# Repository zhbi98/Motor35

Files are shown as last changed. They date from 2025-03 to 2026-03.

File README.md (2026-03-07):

# Motor35

转速-扭矩特性步进电机运用普通的开环控制方式在低速和低负载的情况下可以保持较好的控制精度，但随着负载增大或转速度增加会发生丢步，另一个是转速-扭矩特性让步进电机无法在高转速下稳定工作。

## 特性

在低速状态下，步进电机的扭矩特性曲线通常为水平直线，能够提供较高的扭矩。在高速状态下，由于电感的影响，扭矩特性曲线呈指数下降，导致电机的负载能力显著降低。

> **最大扭矩：** 最大扭矩出现在中低转速范围，随着转速的提高，扭矩会逐渐下降。因为在高频率下，电流流动受到绕组电感的影响，导致电流无法达到稳定值，从而扭矩降低。
> 
> **启动扭矩与连续扭矩：** 启动扭矩指在启动时能够提供的最大扭矩，而连续扭矩则指电机持续运行时能够维持的扭矩。随着脉冲频率的增加，启动扭矩和连续扭矩都会下降。

## 闭环

闭环控制是在开环控制的基础上，增加了 **反馈检测环节**（例如在电机轴增加编码器），形成指令-执行-位置检测-修正的闭环逻辑。解决存在的丢步、偏差、抗干扰能力弱问题，还能提升系统和容错能力。

## FOC 控制

混合式步进电机与无刷电机的内在联系（结构定义相似性，工作原理相似性），所以可以用无刷电机 FOC 的驱动思想驱动步进电机。

结构方面：永磁转子+定子绕组的结构，定子方面：两者都有多相绕组（步进电机通常为两相，无刷电机通常为三相），转子方面：都采用永磁材料制造转子磁极，无刷设计：两者都没有电刷和机械换向器，依靠电子换向。

对于两相步进电机，虽然只有两个绕组，但通常两相绕组是正交的，从而可以简化步骤，省略我们的 clarke 变换，所以其余同样可以采用类似的思路进行一个电流环FOC控制。

    电流检测：对 AB 两相电流进行检测
    Park变换：将 AB 轴静止系转换为dq轴旋转坐标系
    PI调节器：对 Id 和 Iq 进行控制
    Invpark变换：讲 dq 轴转换为AB轴
    SVPWM调制: 输出占空比
    双 H桥驱动：驱动我们的步进电机

这些可以整合到一个驱动器中实现，如下图。这就是一体化集成步进电机闭环驱动器。板上集成磁编码器，具有速度，位置，电流闭环控制功能，适用于 3D 打印机，小型机械臂。

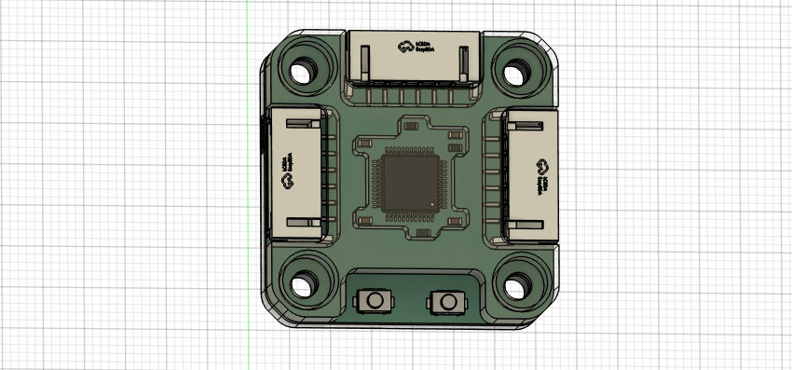
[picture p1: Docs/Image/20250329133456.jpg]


## 硬件

(1) 2 相逆变功率级：东芝凌耐压 50V，载流3.5A 的 PWM 斩波式双全桥电机驱动器，内置带低导通电阻的输出MOSFET（基于成本考虑可以选择其他的型号）。

(2) RS485 收发器：TI 德州仪器 SN75176B（基于成本考虑可以选择其他的型号）。

(3) CAN2.0B 收发器：NXP 恩智浦 High-speed CAN transceiver TJA1051（基于成本考虑可以选择其他的型号）。

(4) 磁编码器：MagnTek 麦歌恩 mt6816 单圈绝对式14位编码器，支持最高转速25Krpm。

(6) 主控 MUC 芯片：意法半导体 STM32F103。

## 关于打样

驱动器板 Motor35（PCB 采用 **4 层板** 设计）：[HardWare/kiacd_project](./HardWare/kiacd_project)

如果想自己修改 PCB 需要安装 KiCad（开源的 EDA 工具，也非常易学），官方下载地址： https://www.kicad.org/。

打样制作可以直接进入到下面这两个路径下：

把 Motor35 Gerber 文件夹 [HardWare/Gerber](./Docs/Motor35-PCB/) 压缩为 Motor35.zip，

把这个 .zip 给 PCB 制造厂即可（例如 JLC，**PCB 经过打样验证，可以放心使用**）。

**器件 BOM 目录**：[HardWare/ibom.html](./Docs/Motor35-BOM.csv)（PCB 没器件位号，按网页交互式 BOM 贴片）。

原理图 PDF 目录： [Docs/Motor35-SCH.csv](Docs/Motor35-SCH.pdf)

## 核心固件

固件主要包括几大功能模块：

- hal 驱动：板载的各种硬件驱动比如 USB、Tim、Can、Spi。
- utils 库：STM32 的 Flash 存储接口，Modbus 协议解析库，软定时器组件。
- drivers：ARM的CMSIS驱动，ST官方的HAL库。
- device：电机H桥驱动，编码器驱动和校准，电机控制核心代码，LED 驱动框架 LedMX 和按键驱动 MultiButton。
- main：上层 Can，Rs485 应用控制协议，用于控制同步电机状态/参数，以及用户设置参数保存功能。

## 编译下载

固件没有使用 ARM Keil 开发，而是先用 CMake 构建出 Makefile，然后再用 arm-gcc 编译（可以自己创建 F103 的 Keil 工程，把 Motor35 组织到 Keil 编译）。

Motor35 用的是 VSCode 搭配 OpenOCD 图形化下载调试，需要下载安装下列工具链：

MiniGW： https://sourceforge.net/projects/mingw-w64/files/

arm-gcc ：[Downloads | GNU Arm Embedded Toolchain Downloads – Arm Developer](https://developer.arm.com/downloads/-/gnu-rm)

openOCD：[Download OpenOCD for Windows](https://gnutoolchains.com/arm-eabi/openocd/)

CMake：[Download CMake](https://cmake.org/download/)

VSCode：[https://code.visualstudio.com/](https://code.visualstudio.com/)

> 安装后具体如何配置使用这些工具，篇幅较长不写在这里，我把具体配置使用方法写在这里：[工具链配置使用方法](https://blog.csdn.net/jf_52001760/article/details/126826393)。

**Motor35 编译步骤**：

把 cmake 脚本 CMakeLists.txt 的目录添加到 `1` 这里，如下图。

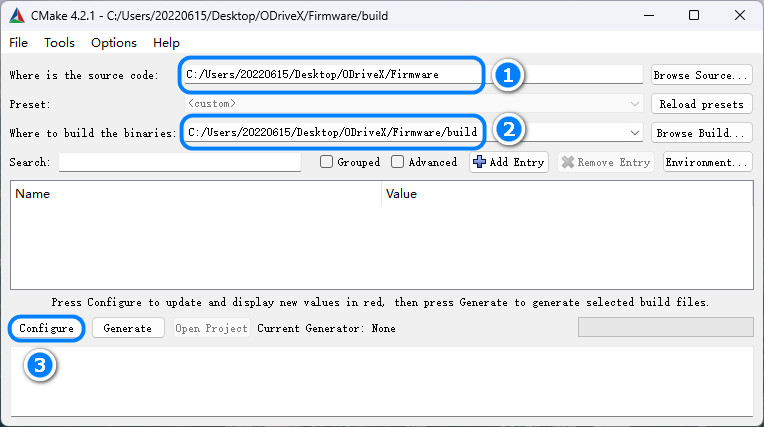
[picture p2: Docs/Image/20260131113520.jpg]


(2) 在 Firmware 目录下创建 build 目录，并指定到 `2` 这里。

(3) 点击 "Configure"，在弹出面板选择目标工程，如下图。

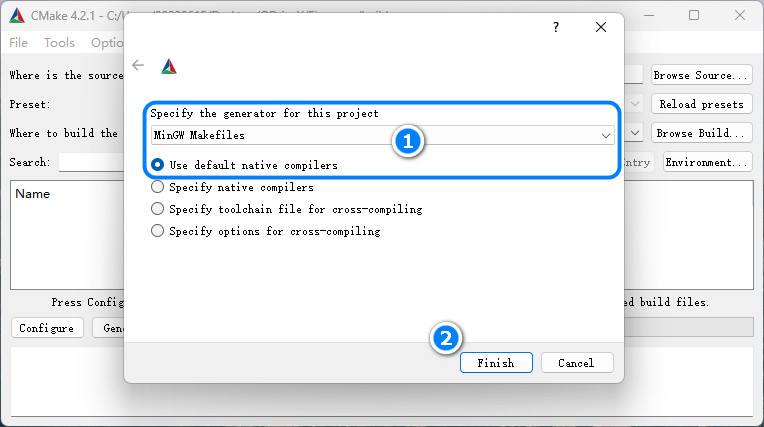
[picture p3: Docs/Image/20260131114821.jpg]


(5) 在 vscode 的命令行 `cd build` 进入`build/`目录，然后执行 make -j2 即可开始编译。

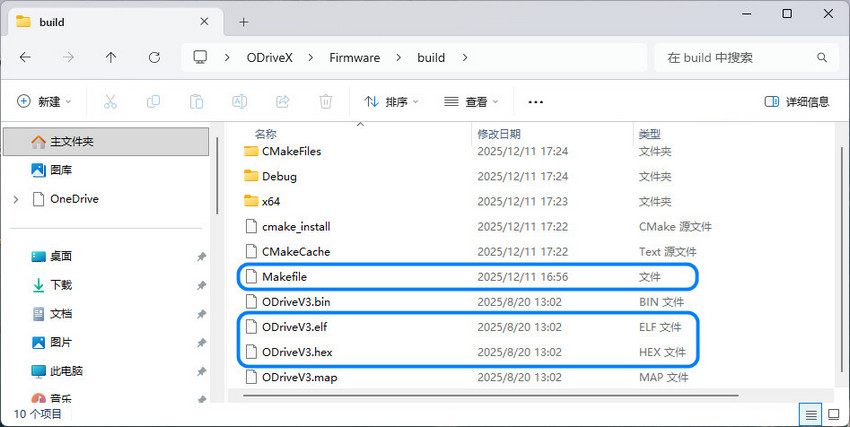
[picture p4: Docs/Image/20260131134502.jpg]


(6) 使用 openOCD 把 `.elf` 文件下载到 Motor35 硬件，下载方法同样参照 [工具链配置使用方法](https://blog.csdn.net/jf_52001760/article/details/126826393)（PCB 上预留了 SWD 调试接口同时支持固件下载）。

## 电机选型

电机可以在淘宝搜索购买，最好购买低相电阻步进电机（较好的电机的相电阻通常为 2-5 Ohm）。相电阻过高可能导致电机在静止时出现高频震动。

电机机身：28MM，出轴直径：5MM (D轴4.5MM)，出轴长度：22MM
静力矩：0.29 N.m，额定电流：1.5 A，电阻：3.0Ohm/相。

> 要实际测量电机相电阻（万用表接到对应相的两个端子测量），比如购买的步进电机在参数描述中标明的相电阻为 2.2 Ohm，实则实际测出的相电阻高达 29 Ohm
> 
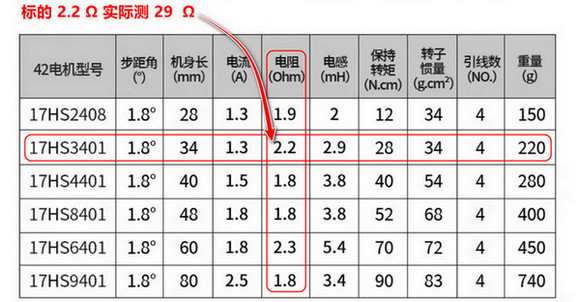
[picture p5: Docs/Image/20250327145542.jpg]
> 

## 编码器安装

在电机轴上安装径向磁铁（用于磁编码器检测），磁铁尺寸 $d=8mm$，$h=2mm$，注意径向磁铁和轴同心度不要过度偏移，让后把驱动器板放到板支架中，用 M3.0 螺丝把驱动器和板定到电机尾部，磁铁与编码器的间隙大概为 $1mm$。

驱动板支架零件目录：[Model](./Model)，把 .step 文件给 3D 打印即可。

## Configuration

固件上已经调试好 Pid 参数，可以适配大多数35步进电机，默认情况下不需要再调试 Pid 电机也能正常工作。Pid 可以用 Can 指令调整（看Can协议部分的说明），方法如下：

- **Kp 的调整**：将 Kd，Ki 置 0，从零开始逐渐增加 Kp，直到系统出现震荡。然后逐渐减小Kp，直到系统不再震荡。Kp 的最终值通常在引起震荡的 Kp 值的 80%-90% 之间。

- **Kd 的调整**：在 Kp 调整稳定后，开始增加 Kd。如果系统在空载时仅需要 Kp，那么在负载情况下可能需要增加 Kd 来减少超调和震荡。

- **Ki 的调整**：如果系统在 Kp 和 Kd 的调整后仍然存在静态误差，可以尝试增加 Ki。但 Ki的值通常很小，需要细致地调整。

配置限制参数，限制参数再 /motor/control_config.h 文件定义，如下。

```c
/********************  硬件配置区  ********************/
#define _Current_Rated_Current  (3000)  /**< 额定电流(mA)*/
#define _Current_Cali_Current   (2000)  /**< 校准电流(mA)*/
/********************  运动参数配置区  ********************/
...
#define _Move_Rated_Speed           ((int32_t)(50 * Move_Pulse_NUM))    /**< (额定转速)(50转每秒)*/
#define _Move_Rated_UpAcc           ((int32_t)(1000 * Move_Pulse_NUM))  /**< (固件额定加速加速度)(1000r/ss)*/
#define _Move_Rated_DownAcc         ((int32_t)(1000 * Move_Pulse_NUM))  /**(固件额定减速加速度)(1000r/ss)*/
#define _Move_Rated_UpCurrentRate   ((int32_t)(20 * _Current_Rated_Current))    /**< (固件额定增流梯度)(20倍额定/s)*/
#define _Move_Rated_DownCurrentRate ((int32_t)(20 * _Current_Rated_Current))    /**< (固件额定减流梯度)(20倍额定/s)*/
```

用户设置在 /main/setup/setup.c 中定义，用户设置参数可以用 Can 指令设置（看Can协议部分的说明）设置后保存在 Flash 掉电保存。

```c
const _setup_t _setup_def = {
    ...
    .can_id = 0x01,
    .home_ofs = 0,
    ...
    .current_down_acc = 2 * 1000, /*(mA/s)*/
    .current_up_acc = 2 * 1000, /*(mA/s)*/
    .current_rated = 1000,
    .cali_current = 2000,
    ...
};
```

## 按键逻辑

(1) 启动停止闭环模式：按键 1 短按一次，启动或停止闭环模式，启动闭环模式的同时会进入默认的模式，例如位置闭环。

(2) 目标清 0：按键 2 短按一次，如果当前控制模式为速度模式，那么按下此时会将目标速度置为 0，位置模式，则将目标位置置为 0。

(3) 电机编码器校准：按键 1 长按两次，校准时电机会慢速正转一圈再反转一圈。

> 按下按键时 LED 跟随闪烁，以指示按键是否响应。

## CAN 协议

一帧 CAN 报文只能传 8 个字节数据，和 11 位的标准 Std-Id，这里把 Std-Id 的低 7 位也用作数据，用来传控制指令字 CMD，控制协议定义如下：



Device Id 占用 4 位，CMD 占用 7 位，协议最多两个参数：参数 1 占用 4 个字节，参数 2 占用 4 个字节。

> 个别协议要两个参数，例如位置控制：设置目标位置和速度限制。

具体指令在[protocols/can_protocol.c](./Firmware/main/protocols/can_protocol.c) 这里定义，具体可以看这个文件，具体控制指令和控制方式查看 [Docs/Protocols](./Docs/Protocols) 目录下相应的协议文档，这里只截取部分。

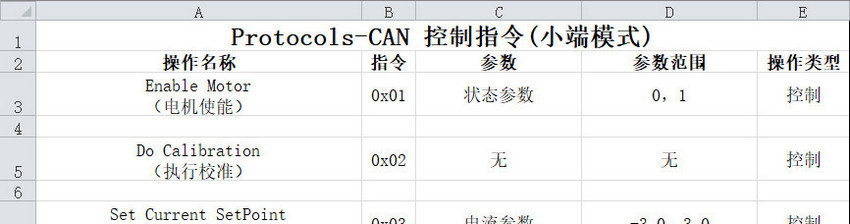
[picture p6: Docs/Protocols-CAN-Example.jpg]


## 震动问题

注意步进驱动器控制步进电机工作在位置环并要求静止在某个固定位置时可能会出现高频震动的问题。引起高频微弱震动的原因是由于在位置环控制模式下，驱动器为了让让电机接近指定位置而控制电机在齿槽间反复微调而产生震动。

> 这个现象排除驱动器的电路问题（比如焊接的电流采样电阻是否正确等等），磁编码器检测磁铁的安装同心度问题（通常同心度要求不是很高，确保不要过度偏移即可）那有极大的可能是步进电机的相电阻过大导致的，可以更换了其他电机进行测试。

如果更换电机测试后发现同一个闭环步进电机驱动器驱动一个步进电机工作在位置环保持静止时工作正常，而驱动另一个步进电机静止时出现高频震动，那可以肯定就是相电阻过高而导致的。出现震动现象的电机相电阻通常为 10-30 Ohm，而较好电机的相电阻通常为 2-5 Ohm。注意检查电机参数可能的虚标，例如购买的步进电机在参数描述中标明的相电阻为 2.2 Ohm，实则实际测出的相电阻高达 29 Ohm，所以电机出现震动现象和线圈相电阻是有一定关系的。

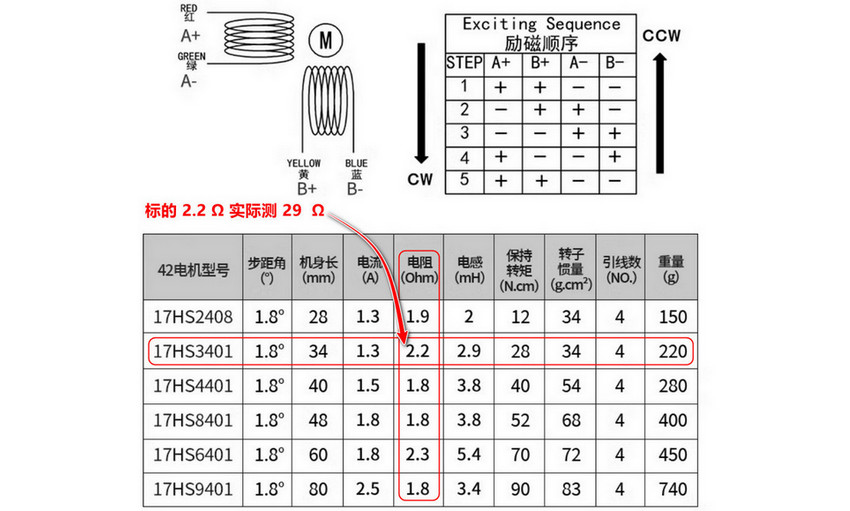
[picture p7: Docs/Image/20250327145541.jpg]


可以通过修改驱动器程序固件来修复这个问题，修改驱动输出部分，在最终 FOC 输出驱动电流部分添加一个系数即可，通过该系数来调节驱动器 FOC 的输出电流（当然调节电流参数会对最终的扭矩有略微的影响，但并不影响闭环精度），如下图。

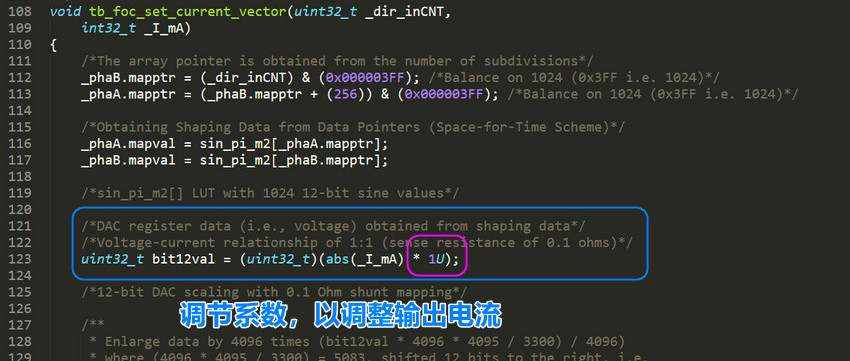
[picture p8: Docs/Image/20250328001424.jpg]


## 控制带宽

电机控制速度/位置积分需要精确节拍，电机控制所有逻辑都是在定时器触发的中断中进行，我设置的中断函数频率较高，达到20KHz，可能会导致 main 主循环不执行。

> **20 kHz 中断**：TIM 每 50 μs 触发一次中断。

**电机控制逻辑较多：** 运行时间合计接近或超过 50 μs，会形成中断几乎连轴转、主循环几乎没机会跑”的情况（和芯片主频无关，只要中断内处理的时间超过中断周期时间就会导致 main 函数不执行）。

> 通过 SPI 阻塞读 MT6816，最多 3 次尝试 × 2 次 16bit 传输，再加 16 位奇偶校验循环。SPI 时钟为 9MHz，仅通信就可能 5-15μs。
> 
> 编码器处理、位置/速度估计、多种运行模式下的控制（DCE/PID/电流等）、运动规划、软目标更新、堵转/过载检测等就需要数十μs。

没有具体要求需要多少控制频率，控制制带宽越高，控制越平滑所以默认设定为 20KHz，若控制带宽允许，可把闭环控制改为 10 kHz 或 5 kHz，中断周期变为 100 μs / 200 μs。

> 这里 20 kHz 不是控制带宽的硬性要求，更多是裕量和步进分辨率。

修改控制频率同时改两处：
motion_planner.h 的  CONTROL_FREQUENCY 定义。
修改电机控制运行中断定时器的中断时间。

```c
/****************************************  控制器频率配置区  ****************************************/
#define CONTROL_FREQ_HZ   (20000)                     /**< 控制频率_hz*/
#define CONTROL_PERIOD_US (1000000 / CONTROL_FREQ_HZ) /**< 控制周期_us*/
```

### 评估控制带宽

(1) motor_control.c 涉及的一阶滤波：由 `等效时间常数由 >> 5`（约 32 个采样）决定。20 kHz 时：32 × 50us =1.6 ms 即控制带宽约 100 Hz。对很多应用来说 50 Hz 左右就足够。

(2) 位置/速度环 (DCE、PID 闭环带宽)：这是外环（位置环、速度环），一般做到几十到一两百 Hz 带宽就足够（位置/速度环 -3 dB 带宽）。 

> 常见经验：**采样率 ≥ 10～20 倍闭环带宽**。 
> 若你目标闭环带宽在 100～200 Hz，**5 kHz 已经够用，2 kHz 是底线**。

(3) FOC/电流指令：由 TB67H450 等驱动接收，5～10 kHz 更新电流给定对多数应用足够。

(4) 运动规划：用 CONTROL_FREQUENCY 做离散积分，频率高一点更平滑，但 5～10 kHz 通常足够平滑。

(5) 控制更新频率：下限约 2～5 kHz（再低速度估计和环路的相位裕量会变差）。推荐 5～10 kHz 在保证控制性能的同时，能给主循环留出明显时间。在需要 **极高步进率** 或 **尽量小的相位延迟** 时才必要 20 kHz。

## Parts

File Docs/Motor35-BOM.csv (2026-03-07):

Reference | Value | Datasheet | Footprint | Qty | DNP
C1,C3,C5,C7,C10,C11,C16 | 0.1uF | ~ | Capacitor_SMD:C_0603_1608Metric | 7
C2,C6 | 22pF | ~ | Capacitor_SMD:C_0603_1608Metric | 2
C4,C8,C17,C26,C31 | 10uF | ~ | Capacitor_SMD:C_0603_1608Metric | 5
C12,C13,C14,C15 | 100nF (104) 10% 50V | ~ | Capacitor_SMD:C_0603_1608Metric | 4
C18 | 100pF(101) 50V | ~ | Capacitor_SMD:C_0603_1608Metric | 1
C19,C20 | 100nF(104) 50V | ~ | Capacitor_SMD:C_0603_1608Metric | 2
C21 | 100nF104 | ~ | Capacitor_SMD:C_0603_1608Metric | 1
C22 | 4.7uF(475) 50V | ~ | Capacitor_SMD:C_1206_3216Metric | 1
C23 | 10uF(106) | ~ | Capacitor_SMD:C_0603_1608Metric | 1
C24 | 47uF(106) | ~ | Capacitor_SMD:C_0603_1608Metric | 1
C27,C28,C29,C30 | 100uF 50V | ~ | Capacitor_SMD:C_1206_3216Metric | 4
C32 | 100nF | ~ | Capacitor_SMD:C_0603_1608Metric | 1
D1 | RED LED | ~ | LED_SMD:LED_0603_1608Metric | 1
D2,D3 | B5819WS | http://www.vishay.com/docs/85622/1n914.pdf | Diode_SMD:D_0805_2012Metric | 2
D4 | SS54 | http://www.vishay.com/docs/85622/1n914.pdf | Diode_SMD:D_SMA | 1
D5 | SMBJ28CA | https://www.vishay.com/docs/88301/15ke.pdf | Diode_SMD:D_SMB | 1
IC1,IC2 | TB67H450FNG,EL | http://toshiba.semicon-storage.com/info/docget.jsp?did=65346&prodName=TB67H450FNG | 3rd_Driver_Motor:SOIC-8_L4.8-W5.8-P1.27_TB67H450FNG | 2
IC3 | MT6816 | http://www.magntek.com.cn/upload/MT6816_Rev.2.0.pdf | 3rd_Sensor_Encoder:SOIC-8_L4.7-W5.8-P1.27_MT6816 | 1
IC4 | ME3116AM6G | https://componentsearchengine.com/Datasheets/1/ME3116AM6G.pdf | 3rd_Converter_DCDC:SOT-23-6_L2.7-W2.2-P0.95_ME3116AM6G | 1
J1 | DBUG |  | 3rd_Connector_JST_SMD:CONN-SMD_1x3P-P1.0-H_WAFER-SH1.0-3PWB | 1
J2 | SWD |  | 3rd_Connector_JST_SMD:CONN-SMD_1x4P-P1.0-H_WAFER-SH1.0-4PWB | 1
J3,J7 | CAN_BUS |  | 3rd_Connector_JST_SMD:CONN-SMD_1x2P-P1.0-H_WAFER-SH1.0-2PWB | 2
J4 | MOTOR |  | 3rd_Connector_JST_SMD:CONN-SMD_1x6P-P2.0-H_WAFER-PH2.0-6PWB | 1
J5,J6 | POWER IN |  | 3rd_Connector_JST_SMD:CONN-SMD_1x6P-P2.0-H_WAFER-PH2.0-6PWB | 2
JP1 | Jump | ~ | Jumper:SolderJumper-2_P1.3mm_Open_RoundedPad1.0x1.5mm | 1
L1 | FCI3216-6R8 6.8uH | ~ | Inductor_SMD:L_1206_3216Metric | 1
R1 | 10M | ~ | Resistor_SMD:R_0603_1608Metric | 1
R2 | 3.3K | ~ | Resistor_SMD:R_0603_1608Metric | 1
R5,R9,R10,TH1 | 10K | ~ | Resistor_SMD:R_0603_1608Metric | 4
R8 | 1k | ~ | Resistor_SMD:R_0603_1608Metric | 1
R11,R12,R13,R14 | 1KΩ (1001) ±1% | ~ | Resistor_SMD:R_0603_1608Metric | 4
R15,R16 | 0.1Ω (R100) ±1% | ~ | Resistor_SMD:R_1206_3216Metric | 2
R17 | 1.91k(1901) | ~ | Resistor_SMD:R_0603_1608Metric | 1
R18 | 10k(1002) | ~ | Resistor_SMD:R_0603_1608Metric | 1
R19 | 1M | ~ | Resistor_SMD:R_0603_1608Metric | 1
R22 | 120R | ~ | Resistor_SMD:R_0603_1608Metric | 1
S1,S2 | KEY-PB_4P_MIN |  | 3rd_Button_Switch_SMD:KEY-SMD_2P_L4.0-W3.0-V_K2-1807SN-A3DW-06 | 2
U1 | XC6206P332MR | https://www.torexsemi.com/file/xc6206/XC6206.pdf | Package_TO_SOT_SMD:SOT-23 | 1
U2 | STM32F103CBTx | https://www.st.com/resource/en/datasheet/stm32f103cb.pdf | Package_QFP:LQFP-48_7x7mm_P0.5mm | 1
U3 | TJA1051T |  | 3rd_Interface_CAN:SOT96_L5.0-W4.0-P1.27_TJA1051 | 1
Y1 | 3225 8M 12PF 10PPM | ~ | Crystal:Crystal_SMD_3225-4Pin_3.2x2.5mm | 1

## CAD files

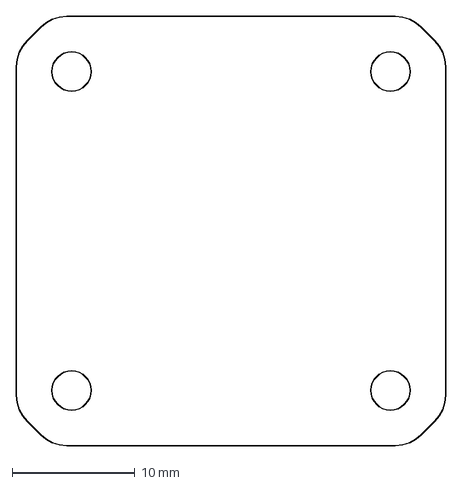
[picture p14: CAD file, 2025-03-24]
HardWare/EDG.dxf
35.0 x 35.0 mm

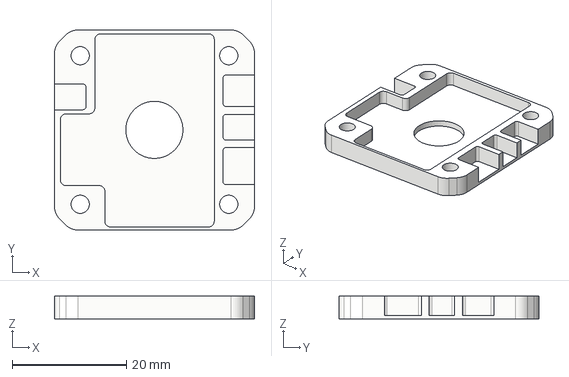
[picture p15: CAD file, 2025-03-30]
Model/Motor35SUP.step
35.0 x 35.0 x 4.00 mm

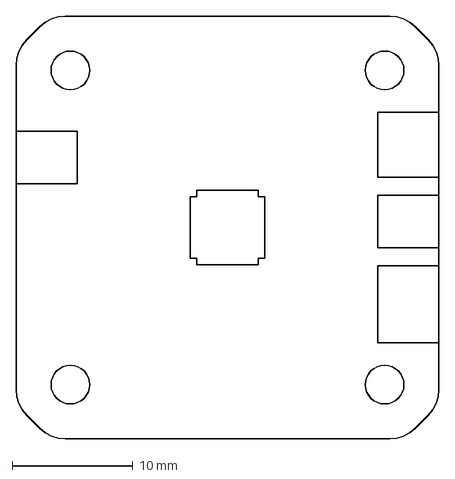
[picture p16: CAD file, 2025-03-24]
HardWare/BOM.dxf
35.0 x 35.0 mm

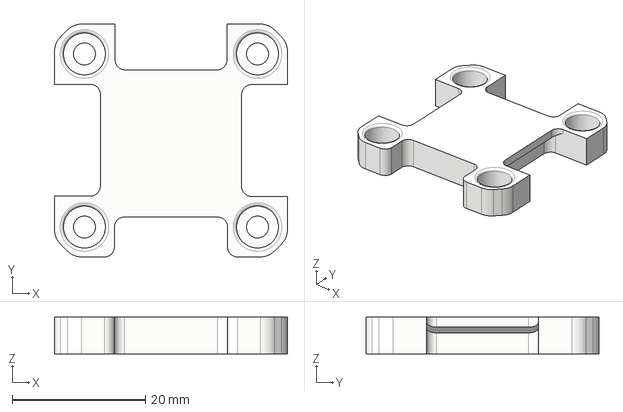
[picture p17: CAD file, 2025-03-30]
Model/Motor35OVER.step
35.0 x 35.0 x 5.55 mm

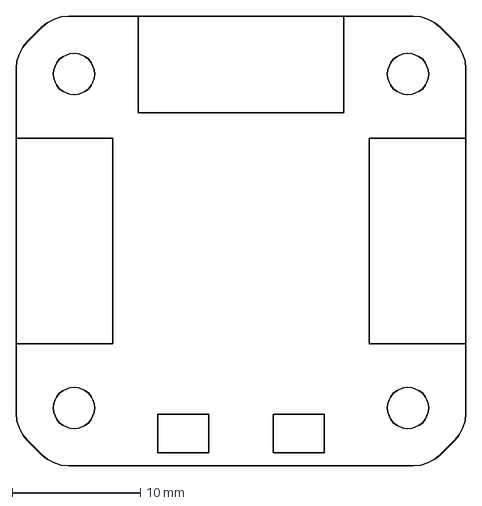
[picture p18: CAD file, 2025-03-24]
HardWare/TOP.dxf
35.0 x 35.0 mm

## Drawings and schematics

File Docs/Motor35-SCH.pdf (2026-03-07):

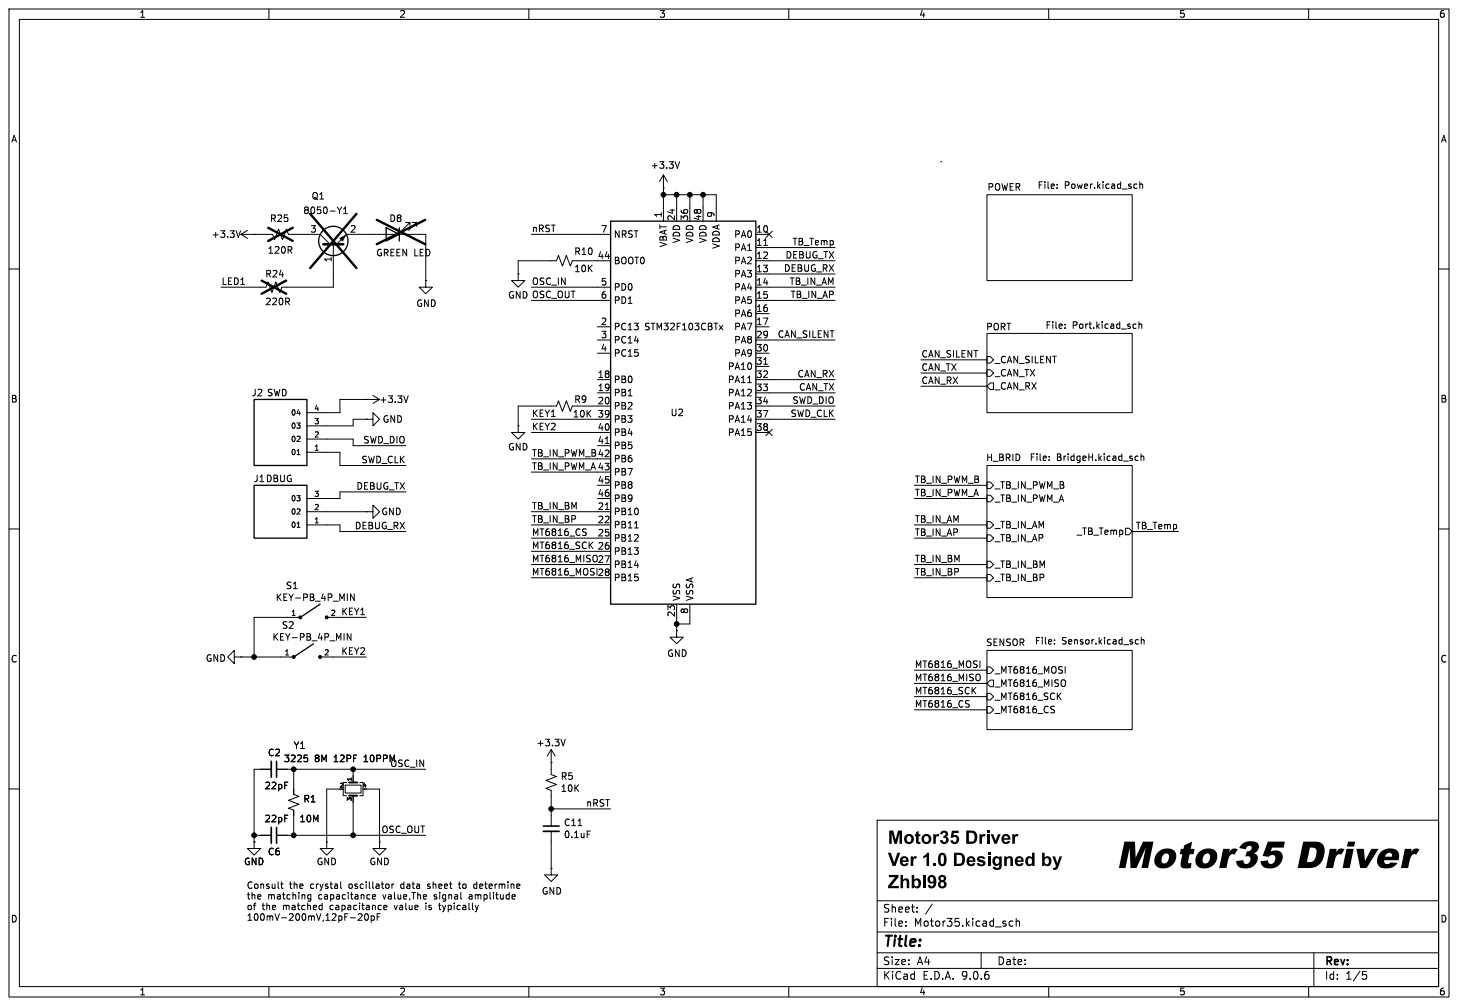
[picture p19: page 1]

1 VDD 24 VSS 23 VDD 36 VSSA

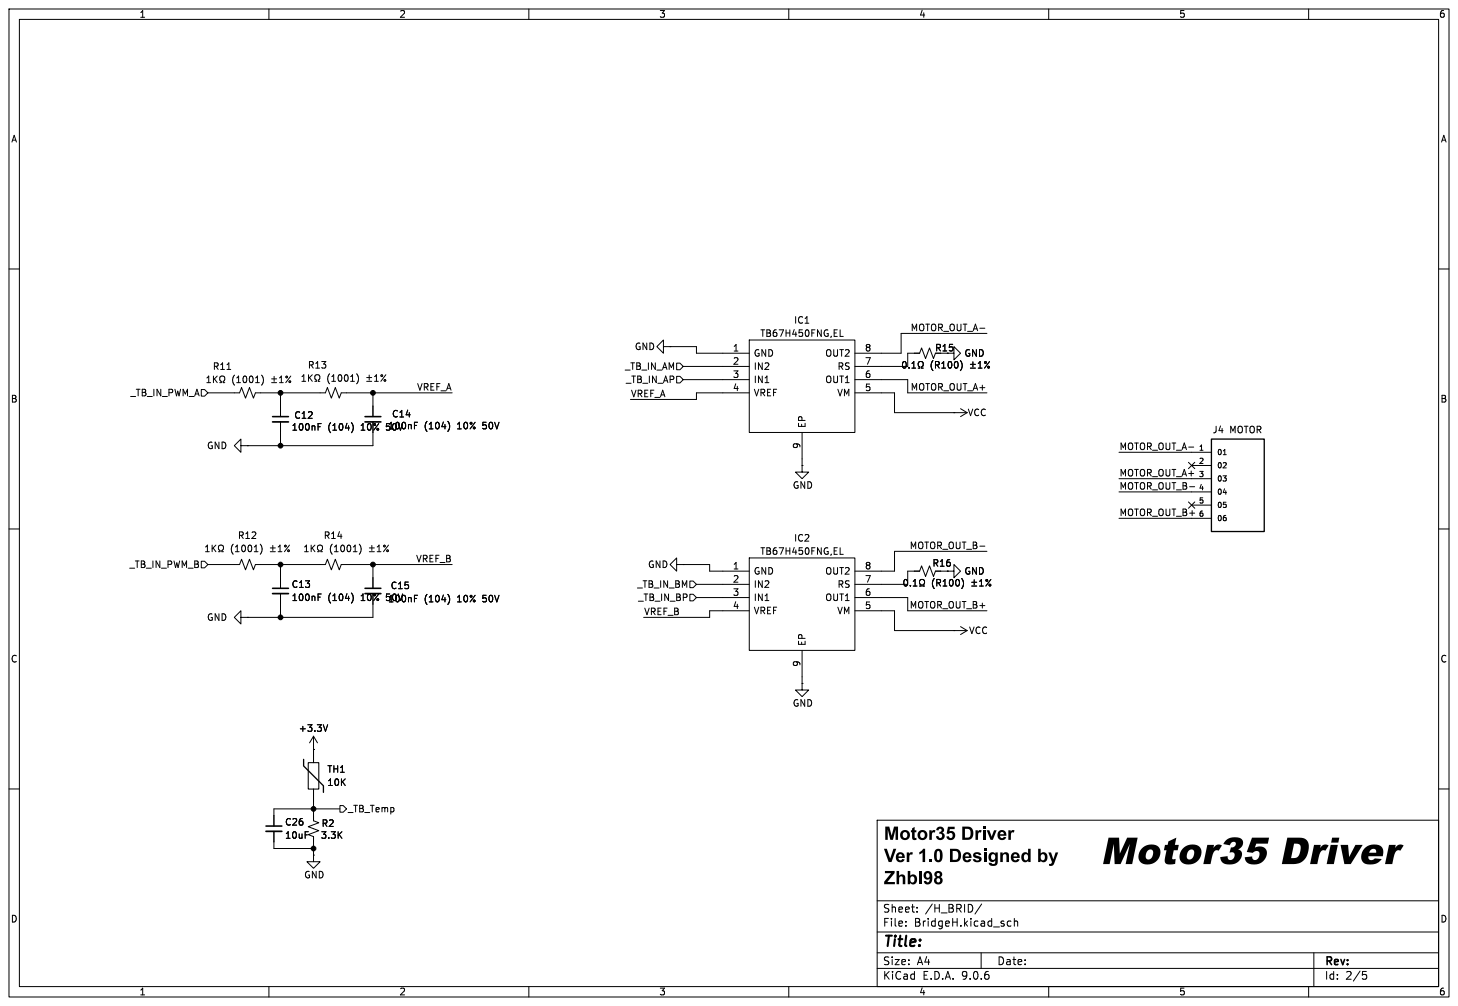
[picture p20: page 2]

Id: 2/5 Title: File: BridgeH.kicad_sch Sheet: /H_BRID/ GND

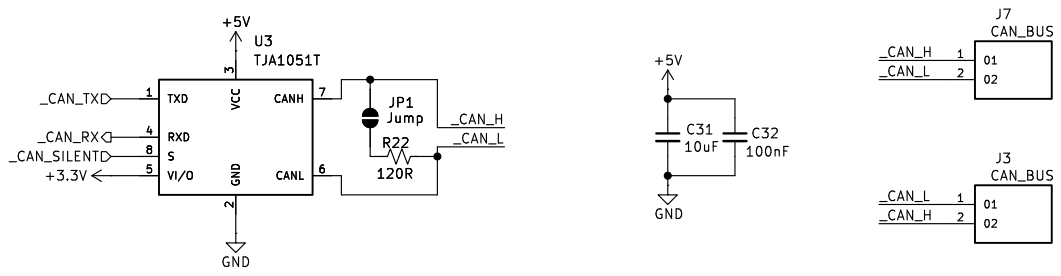
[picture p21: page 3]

Id: 3/5 Title: File: Port.kicad_sch Sheet: /PORT/

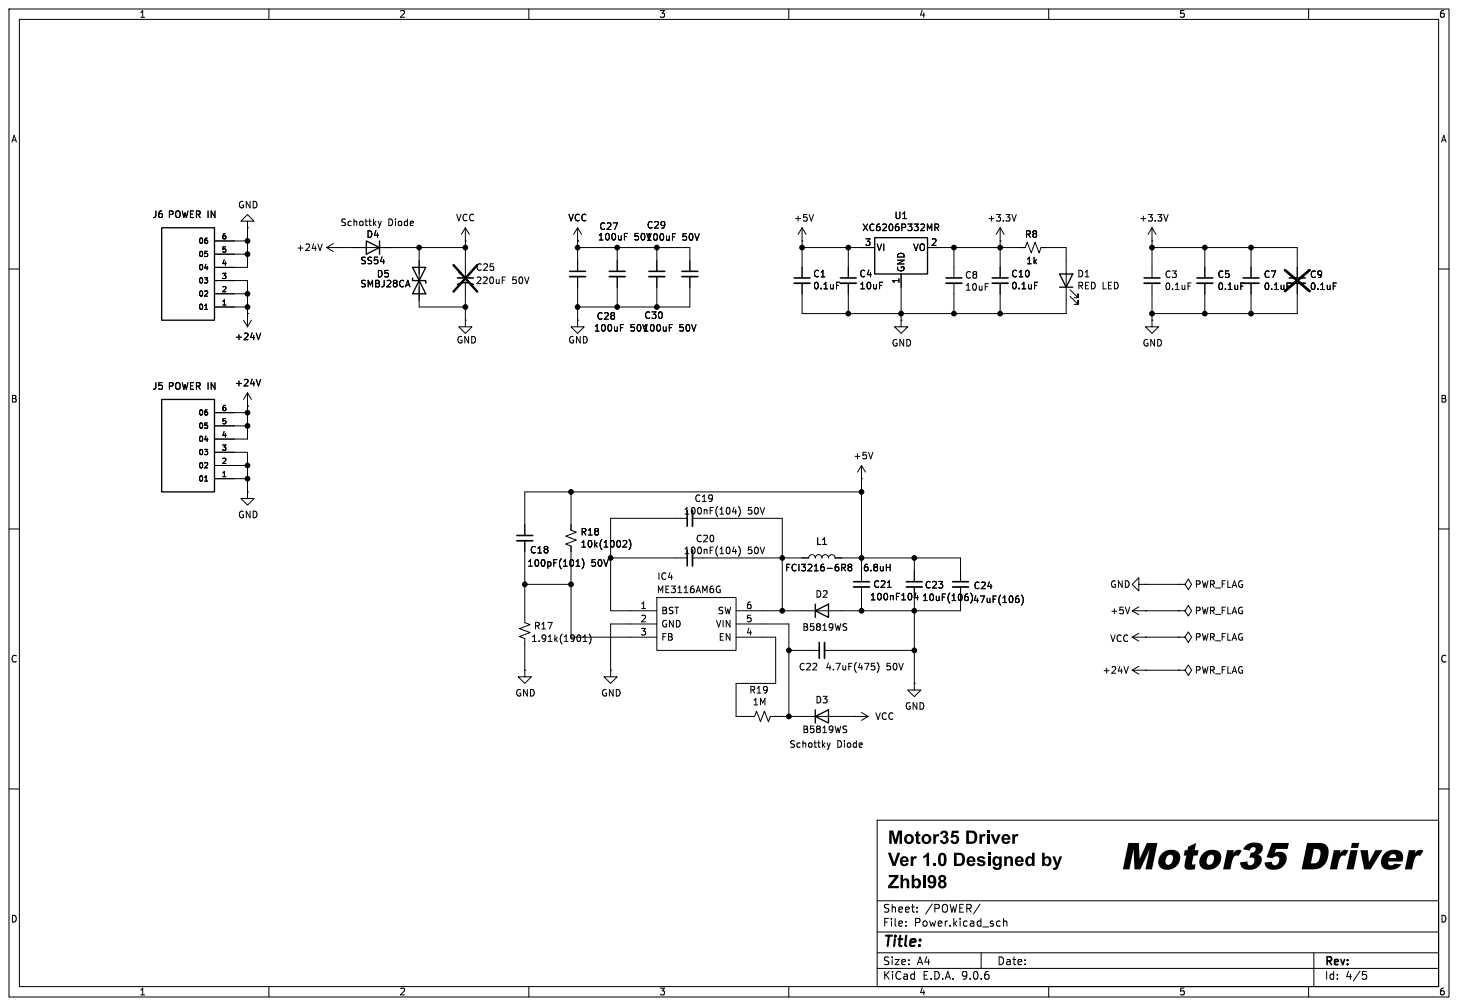
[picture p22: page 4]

Id: 4/5 Title: File: Power.kicad_sch Sheet: /POWER/ GND

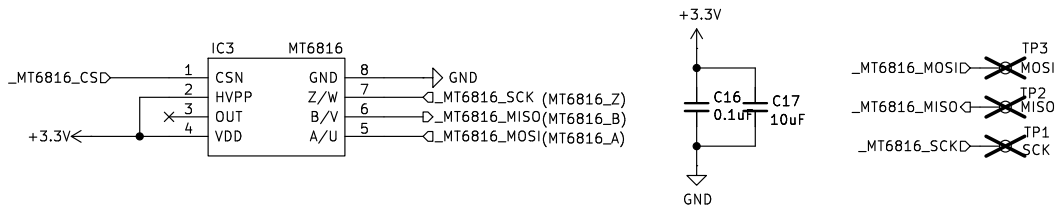
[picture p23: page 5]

Id: 5/5 Title: File: Sensor.kicad_sch Sheet: /SENSOR/

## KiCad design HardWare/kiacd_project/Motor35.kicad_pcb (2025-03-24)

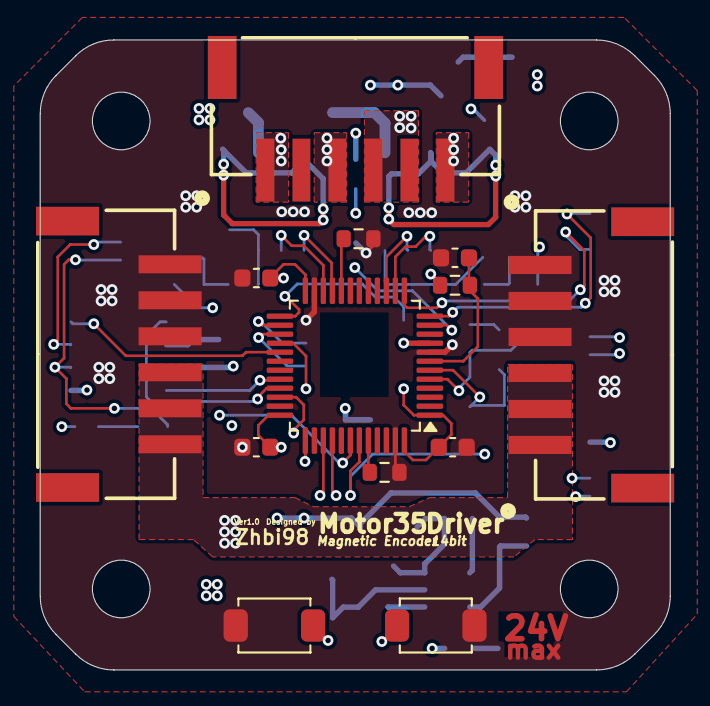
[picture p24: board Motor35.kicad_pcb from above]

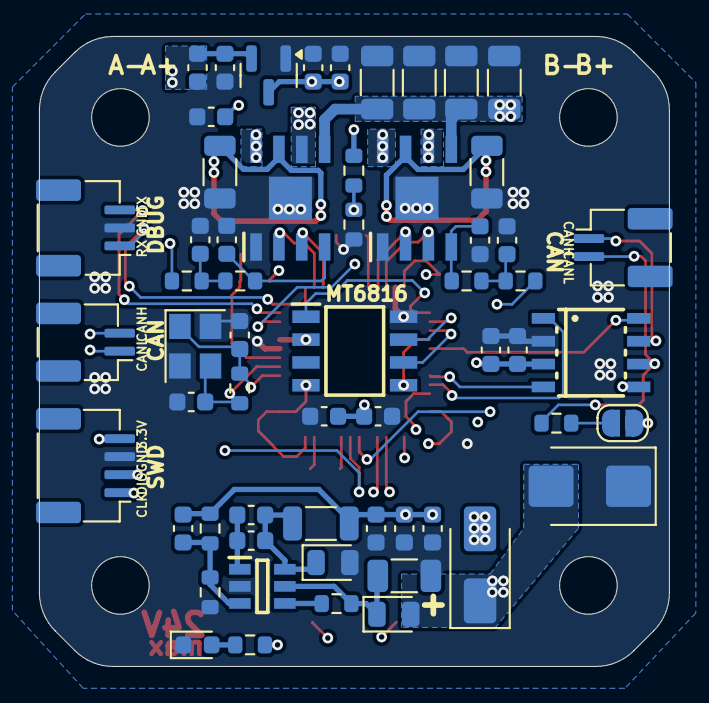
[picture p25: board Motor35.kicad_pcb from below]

Board: 4 copper layers, 35.0 x 35.0 mm, 71 parts (58 on the bottom side), 49 nets.

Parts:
C1, C3, C5, C7, C10, C11, C16: 0.1uF; C_0603_1608Metric
C2, C6: 22pF; C_0603_1608Metric
C4, C8, C17, C26, C31: 10uF; C_0603_1608Metric
C12, C13, C14, C15: 100nF (104) 10% 50V; C_0603_1608Metric
C18: 100pF(101) 50V; C_0603_1608Metric
C19, C20: 100nF(104) 50V; C_0603_1608Metric
C21: 100nF104; C_0603_1608Metric
C22: 4.7uF(475) 50V; C_1206_3216Metric
C23: 10uF(106); C_0603_1608Metric
C24: 47uF(106); C_0603_1608Metric
C27, C28, C29, C30: 100uF 50V; C_1206_3216Metric
C32: 100nF; C_0603_1608Metric
D1: RED LED; LED_0603_1608Metric
D2, D3: B5819WS; D_0805_2012Metric
D4: SS54; D_SMA
D5: SMBJ28CA; D_SMB
IC1, IC2: TB67H450FNG,EL; SOIC-8_L4.8-W5.8-P1.27_TB67H450FNG
IC3: MT6816; SOIC-8_L4.7-W5.8-P1.27_MT6816
IC4: ME3116AM6G; SOT-23-6_L2.7-W2.2-P0.95_ME3116AM6G
J1: DBUG; CONN-SMD_1x3P-P1.0-H_WAFER-SH1.0-3PWB
J2: SWD; CONN-SMD_1x4P-P1.0-H_WAFER-SH1.0-4PWB
J3, J7: CAN_BUS; CONN-SMD_1x2P-P1.0-H_WAFER-SH1.0-2PWB
J4: MOTOR; CONN-SMD_1x6P-P2.0-H_WAFER-PH2.0-6PWB
J5, J6: POWER IN; CONN-SMD_1x6P-P2.0-H_WAFER-PH2.0-6PWB
JP1: Jump; SolderJumper-2_P1.3mm_Open_RoundedPad1.0x1.5mm
L1: FCI3216-6R8 6.8uH; L_1206_3216Metric
R1: 10M; R_0603_1608Metric
R2: 3.3K; R_0603_1608Metric
R5, R9, R10: 10K; R_0603_1608Metric
R8: 1k; R_0603_1608Metric
R11, R12, R13, R14: 1KΩ (1001) ±1%; R_0603_1608Metric
R15, R16: 0.1Ω (R100) ±1%; R_1206_3216Metric
R17: 1.91k(1901); R_0603_1608Metric
R18: 10k(1002); R_0603_1608Metric
R19: 1M; R_0603_1608Metric
R22: 120R; R_0603_1608Metric
S1, S2: KEY-PB_4P_MIN; KEY-SMD_2P_L4.0-W3.0-V_K2-1807SN-A3DW-06
TH1: 10K; R_0603_1608Metric
U1: XC6206P332MR; SOT-23
U2: STM32F103CBTx; LQFP-48_7x7mm_P0.5mm
U3: TJA1051T; SOT96_L5.0-W4.0-P1.27_TJA1051
Y1: 3225 8M 12PF 10PPM; Crystal_SMD_3225-4Pin_3.2x2.5mm

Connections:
+3.3V: C3.1, C5.1, C7.1, C8.1, C10.1, C16.1, C17.1, IC3.2 (HVPP), IC3.4 (VDD), J2.4, R5.1, R8.1, TH1.1, U1.2 (VO), U2.1 (VBAT), U2.9 (VDDA), U2.24 (VDD), U2.36 (VDD), U2.48 (VDD), U3.5 (VI/O)
+5V: C1.1, C4.1, C18.1, C21.1, C23.1, C24.1, C31.1, C32.1, L1.2, R18.1, U1.3 (VI), U3.3 (VCC)
+24V: D4.2 (A), J5.4, J5.5, J5.6, J6.1, J6.2, J6.3
/CAN_RX: U2.32 (PA11), U3.4 (RXD)
/CAN_SILENT: U2.29 (PA8), U3.8 (S)
/CAN_TX: U2.33 (PA12), U3.1 (TXD)
/DEBUG_RX: J1.1, U2.13 (PA3)
/DEBUG_TX: J1.3, U2.12 (PA2)
/H_BRID/MOTOR_OUT_A+: IC1.6 (OUT1), J4.3
/H_BRID/MOTOR_OUT_A-: IC1.8 (OUT2), J4.1
/H_BRID/MOTOR_OUT_B+: IC2.6 (OUT1), J4.6
/H_BRID/MOTOR_OUT_B-: IC2.8 (OUT2), J4.4
/H_BRID/VREF_A: C14.1, IC1.4 (VREF), R13.2
/H_BRID/VREF_B: C15.1, IC2.4 (VREF), R14.2
/KEY1: S1.2, U2.39 (PB3)
/KEY2: S2.2, U2.40 (PB4)
/MT6816_CS: IC3.1 (CSN), U2.25 (PB12)
/MT6816_MISO: IC3.6 (B/V), U2.27 (PB14)
/MT6816_MOSI: IC3.5 (A/U), U2.28 (PB15)
/MT6816_SCK: IC3.7 (Z/W), U2.26 (PB13)
/OSC_IN: C2.1, R1.2, U2.5 (PD0), Y1.1
/OSC_OUT: C6.1, R1.1, U2.6 (PD1), Y1.3
/PORT/_CAN_H: J3.2, J7.1, JP1.1 (A), U3.7 (CANH)
/PORT/_CAN_L: J3.1, J7.2, R22.2, U3.6 (CANL)
/SWD_CLK: J2.1, U2.37 (PA14)
/SWD_DIO: J2.2, U2.34 (PA13)
/TB_IN_AM: IC1.2 (IN2), U2.14 (PA4)
/TB_IN_AP: IC1.3 (IN1), U2.15 (PA5)
/TB_IN_BM: IC2.2 (IN2), U2.21 (PB10)
/TB_IN_BP: IC2.3 (IN1), U2.22 (PB11)
/TB_IN_PWM_A: R11.1, U2.43 (PB7)
/TB_IN_PWM_B: R12.1, U2.42 (PB6)
/TB_Temp: C26.1, R2.2, TH1.2, U2.11 (PA1)
/nRST: C11.1, R5.2, U2.7 (NRST)
GND: C1.2, C2.2, C3.2, C4.2, C5.2, C6.2, C7.2, C8.2, C10.2, C11.2, C12.2, C13.2, C14.2, C15.2, C16.2, C17.2, C21.2, C22.2, C23.2, C24.2, C26.2, C27.2, C28.2, C29.2, C30.2, C31.2, C32.2, D1.1 (K), D2.2 (A), D5.1 (A1), IC1.1 (GND), IC1.9 (EP), IC2.1 (GND), IC2.9 (EP), IC3.8 (GND), IC4.2 (GND), J1.2, J2.3, J5.1, J5.2, J5.3, J6.4, J6.5, J6.6, R2.1, R9.2, R10.2, R15.2, R16.2, R17.2, S1.1, S2.1, U1.1 (GND), U2.8 (VSSA), U2.23 (VSS), U2.35 (VSS), U2.47 (VSS), U3.2 (GND), Y1.2, Y1.4
unnamed: C12.1, R11.2, R13.1
unnamed: C13.1, R12.2, R14.1
unnamed: D1.2 (A), R8.2
unnamed: C19.2, C20.2, D2.1 (K), IC4.6 (SW), L1.1
unnamed: C22.1, D3.1 (K), IC4.5 (VIN), R19.2
unnamed: IC1.7 (RS), R15.1
unnamed: IC2.7 (RS), R16.1
unnamed: C19.1, C20.1, IC4.1 (BST)
unnamed: IC4.4 (EN), R19.1
unnamed: C18.2, IC4.3 (FB), R17.1, R18.2
unnamed: JP1.2 (B), R22.1
unnamed: R10.1, U2.44 (BOOT0)
unnamed: R9.1, U2.20 (PB2)
VCC: C27.1, C28.1, C29.1, C30.1, D3.2 (A), D4.1 (K), D5.2 (A2), IC1.5 (VM), IC2.5 (VM)

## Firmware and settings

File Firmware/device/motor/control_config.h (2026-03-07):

/******
	************************************************************************
	******
	** @project : XDrive_Step
	** @brief   : Stepper motor with multi-function interface and closed loop function. 
	** @brief   : 具有多功能接口和闭环功能的步进电机
	** @author  : unlir (知不知啊)
	** @contacts: QQ.1354077136
	******
	** @address : https://github.com/unlir/XDrive
	******
	************************************************************************
	******
	** {Stepper motor with multi-function interface and closed loop function.}
	** Copyright (c) {2020}  {unlir(知不知啊)}
	** 
	** This program is free software: you can redistribute it and/or modify
	** it under the terms of the GNU General Public License as published by
	** the Free Software Foundation, either version 3 of the License, or
	** (at your option) any later version.
	** 
	** This program is distributed in the hope that it will be useful,
	** but WITHOUT ANY WARRANTY; without even the implied warranty of
	** MERCHANTABILITY or FITNESS FOR A PARTICULAR PURPOSE.  See the
	** GNU General Public License for more details.
	** 
	** You should have received a copy of the GNU General Public License
	** along with this program.  If not, see <http://www.gnu.org/licenses/>.
	******
	************************************************************************
******/

/*****
  ** @file     : control_config.c/h
  ** @brief    : 控制配置
  ** @versions : 2.2.3
  ** @time     : 2020/09/15
  ** @reviser  : unli (HeFei China)
  ** @explain  : null
*****/

#ifndef CONTROL_CONFIG_H
#define CONTROL_CONFIG_H

#ifdef __cplusplus
extern "C" {
#endif

#include <stdint.h>
#include <stdbool.h>

/********************  硬件配置区  ********************/
#define _Current_Rated_Current  (3000)  /**< 额定电流(mA)*/
#define _Current_Cali_Current   (2000)  /**< 校准电流(mA)*/

/********************  运动参数配置区  ********************/
#define Move_Step_NUM               ((int32_t)(200))  /**< (使用的电机单圈步数)(每步磁场旋转90°)*/
#define Move_Divide_NUM             ((int32_t)(256))  /**< (每步柔性件控制细分量)*/
#define Move_Pulse_NUM              ((int32_t)(Move_Step_NUM * Move_Divide_NUM))  /**< (电机单圈脉冲数)*/
#define _Move_Rated_Speed           ((int32_t)(50 * Move_Pulse_NUM))    /**< (额定转速)(50转每秒)*/
#define _Move_Rated_UpAcc           ((int32_t)(1000 * Move_Pulse_NUM))  /**< (固件额定加速加速度)(1000r/ss)*/
#define _Move_Rated_DownAcc         ((int32_t)(1000 * Move_Pulse_NUM))  /**(固件额定减速加速度)(1000r/ss)*/
#define _Move_Rated_UpCurrentRate   ((int32_t)(20 * _Current_Rated_Current))	/**< (固件额定增流梯度)(20倍额定/s)*/
#define _Move_Rated_DownCurrentRate	((int32_t)(20 * _Current_Rated_Current))	/**< (固件额定减流梯度)(20倍额定/s)*/

/****************************************  控制器频率配置区  ****************************************/
#define CONTROL_FREQ_HZ   (10000)                     /**< 控制频率_hz*/
#define CONTROL_PERIOD_US (1000000 / CONTROL_FREQ_HZ) /**< 控制周期_us*/

/*void Control_Config_Init_Static(void);  // 控制静态配置*/
/*void Control_Config_Init_Dynamic(void); // 控制动态配置*/

/********************  可变硬件配置区  ************************/
extern int32_t Current_Rated_Current; /**< 额定电流(mA)*/
extern int32_t Current_Cali_Current;  /**< 校准电流(mA)*/

/********************  可变运动参数配置区  ********************/
extern int32_t Move_Home_Offset;
extern int32_t Move_Rated_Speed;           /**< (额定转速)(50转每秒)*/
extern int32_t Move_Rated_UpAcc;           /**< (固件额定加速加速度)(1000r/ss)*/
extern int32_t Move_Rated_DownAcc;         /**< (固件额定减速加速度)(1000r/ss)*/
extern int32_t Move_Rated_UpCurrentRate;   /**< (固件额定增流梯度)(20倍额定/s)*/
extern int32_t Move_Rated_DownCurrentRate; /**< (固件额定减流梯度)(20倍额定/s)*/

#ifdef __cplusplus
}
#endif

#endif

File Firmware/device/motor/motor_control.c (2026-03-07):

/******
	************************************************************************
	******
	** @project : XDrive_Step
	** @brief   : Stepper motor with multi-function interface and closed loop function. 
	** @brief   : 具有多功能接口和闭环功能的步进电机
	** @author  : unlir (知不知啊)
	** @contacts: QQ.1354077136
	******
	** @address : https://github.com/unlir/XDrive
	******
	************************************************************************
	******
	** {Stepper motor with multi-function interface and closed loop function.}
	** Copyright (c) {2020}  {unlir(知不知啊)}
	** 
	** This program is free software: you can redistribute it and/or modify
	** it under the terms of the GNU General Public License as published by
	** the Free Software Foundation, either version 3 of the License, or
	** (at your option) any later version.
	** 
	** This program is distributed in the hope that it will be useful,
	** but WITHOUT ANY WARRANTY; without even the implied warranty of
	** MERCHANTABILITY or FITNESS FOR A PARTICULAR PURPOSE.  See the
	** GNU General Public License for more details.
	** 
	** You should have received a copy of the GNU General Public License
	** along with this program.  If not, see <http://www.gnu.org/licenses/>.
	******
	************************************************************************
******/

/*****
  ** @file     : control_config.c/h
  ** @brief    : 电机控制
  ** @versions : 2.2.3
  ** @time     : 2020/09/15
  ** @reviser  : unli (HeFei China)
  ** @explain  : null
*****/

/*Oneself*/
#include "motor_control.h"

/*Base_Drivers*/
#include "mt6816.h"
#include "tb67h450.h"/*#include "hw_elec.h"*/
/*#include "signal_port.h"*/
#include "enc_cali.h"
#include "temp.h"

/*Control*/
#include "control_config.h"
#include "Location_Tracker.h"
#include "Speed_Tracker.h"
#include "Current_Tracker.h"
#include "Move_Reconstruct.h"
#include "Location_Interp.h"

/****************************************  电流输出(电流控制)  ****************************************/
/****************************************  电流输出(电流控制)  ****************************************/
/**
  * @brief  电流输出
  * @param  current: 输出电流
  * @retval NULL
**/
void Control_Cur_To_Electric(int16_t current)
{
	//输出FOC电流
	motor_control.foc_current = current;
	//输出FOC位置
	if(motor_control.foc_current > 0)				motor_control.foc_location = motor_control.est_location + Move_Divide_NUM;
	else if(motor_control.foc_current < 0)	motor_control.foc_location = motor_control.est_location - Move_Divide_NUM;
	else																		motor_control.foc_location = motor_control.est_location;
	//输出任务到驱动
	tb_foc_set_current_vector(motor_control.foc_location, motor_control.foc_current);
	//CurrentControl_Out_FeedTrack(motor_control.foc_location, motor_control.foc_current, false, true);
}

/****************************************  PID控制(速度控制)  ****************************************/
/****************************************  PID控制(速度控制)  ****************************************/
//PID控制
Control_PID_Typedef pid;

/**
  * @brief  参数配置
  * @param  _k
  * @retval NULL
**/
void Control_PID_SetKP(uint16_t _k)
{
	if(_k <= 1024){		pid.kp = _k;		pid.valid_kp = true;		}
	else{															pid.valid_kp = false;		}
}

/**
  * @brief  参数配置
  * @param  _k
  * @retval NULL
**/
void Control_PID_SetKI(uint16_t _k)
{
	if(_k <= 1024){		pid.ki = _k;		pid.valid_ki = true;		}
	else{															pid.valid_ki = false;		}
}

/**
  * @brief  参数配置
  * @param  _k
  * @retval NULL
**/
void Control_PID_SetKD(uint16_t _k)
{
	if(_k <= 1024){		pid.kd = _k;		pid.valid_kd = true;		}
	else{															pid.valid_kd = false;		}
}

/**
  * @brief  PID参数恢复
  * @param  NULL
  * @retval NULL
**/
void Control_PID_Set_Default(void)
{
	Control_PID_SetKP(De_PID_KP);
	Control_PID_SetKI(De_PID_KI);
	Control_PID_SetKD(De_PID_KD);
}

/**
  * @brief  控制器PID初始化
  * @param  NULL
  * @retval NULL
**/
void Control_PID_Init(void)
{
	//前置配置无效时,加载默认配置
	if(!pid.valid_kp)				{	Control_PID_SetKP(De_PID_KP);		}
	if(!pid.valid_ki)				{	Control_PID_SetKI(De_PID_KI);		}
	if(!pid.valid_kd)				{	Control_PID_SetKD(De_PID_KD);		}
	
	//控制参数
	pid.v_error = 0;	pid.v_error_last = 0;
	pid.op = 0;				pid.oi = 0;			pid.od = 0;	
	pid.i_mut = 0;		pid.i_dec = 0;
	pid.out = 0;
}

/**
  * @brief  PID电流控制
  * @param  _speed    控制速度
  * @retval NULL
**/
void Control_PID_To_Electric(int32_t _speed)
{
	//误差
	pid.v_error_last = pid.v_error;
	pid.v_error = _speed - motor_control.est_speed;	//速度误差
	if(pid.v_error > ( 1024 * 1024))	pid.v_error = ( 1024 * 1024);
	if(pid.v_error < (-1024 * 1024))	pid.v_error = (-1024 * 1024);
	//op输出（比例项）
	pid.op = ((pid.kp) * (pid.v_error));
	//oi输出（积分项，速度误差的积分，通过累加实现，
	//通过右移操作进行衰减，防止积分饱和）
	pid.i_mut += ((pid.ki) * (pid.v_error));
	pid.i_dec  = (pid.i_mut >> 10);
	pid.i_mut -= (pid.i_dec << 10);
	pid.oi    += (pid.i_dec);
	if(pid.oi >      (  Current_Rated_Current << 10 ))	pid.oi = (  Current_Rated_Current << 10 );	//限制为额定电流 * 1024
	else if(pid.oi < (-(Current_Rated_Current << 10)))	pid.oi = (-(Current_Rated_Current << 10));	//限制为额定电流 * 1024
	//od输出（微分项，注意将微分项应用于速度误差的差值)
	pid.od = (pid.kd) * (pid.v_error - pid.v_error_last);
	//综合输出计算（同时限制输出范围，限制最终输出电流在额定电流范围内）
	pid.out = (pid.op + pid.oi + pid.od) >> 10;
	if(pid.out > 			Current_Rated_Current)		pid.out =  Current_Rated_Current;
	else if(pid.out < -Current_Rated_Current)		pid.out = -Current_Rated_Current;
	
	//输出FOC电流
	motor_control.foc_current = pid.out;
	//输出FOC位置
	if(motor_control.foc_current > 0)				motor_control.foc_location = motor_control.est_location + Move_Divide_NUM;
	else if(motor_control.foc_current < 0)	motor_control.foc_location = motor_control.est_location - Move_Divide_NUM;
	else																		motor_control.foc_location = motor_control.est_location;
	//输出任务到驱动
	tb_foc_set_current_vector(motor_control.foc_location, motor_control.foc_current);
	//CurrentControl_Out_FeedTrack(motor_control.foc_location, motor_control.foc_current, false, true);
}

/****************************************  DCE控制器(位置控制)  ****************************************/
/****************************************  DCE控制器(位置控制)  ****************************************/
//DCE控制
Control_DCE_Typedef dce;

/**
  * @brief  参数配置
  * @param  _k
  * @retval NULL
**/
void Control_DCE_SetKP(uint16_t _k)
{
	if(_k <= 1024){		dce.kp = _k;		dce.valid_kp = true;		}
	else{															dce.valid_kp = false;		}
}

/**
  * @brief  参数配置
  * @param  _k
  * @retval NULL
**/
void Control_DCE_SetKI(uint16_t _k)
{
	if(_k <= 1024){		dce.ki = _k;		dce.valid_ki = true;		}
	else{															dce.valid_ki = false;		}
}

/**
  * @brief  参数配置
  * @param  _k
  * @retval NULL
**/
void Control_DCE_SetKV(uint16_t _k)
{
	if(_k <= 1024){		dce.kv = _k;		dce.valid_kv = true;		}
	else{															dce.valid_kv = false;		}
}

/**
  * @brief  参数配置
  * @param  _k
  * @retval NULL
**/
void Control_DCE_SetKD(uint16_t _k)
{
	if(_k <= 1024){		dce.kd = _k;		dce.valid_kd = true;		}
	else{															dce.valid_kd = false;		}
}
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

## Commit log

2025-03-30 更新问题说明
    [Motor35OVER.step, Motor35SUP.step]
2025-04-09 移除ADC,DMA中断，减小ARM芯片负载
2025-04-14 位置环控制时调节到达目标位置的额定速度和时间，新额定速度，过程时间未生效问题
2025-07-20 Can not set the acceleration, otherwise the mode switching speed can not be limited in time.
    Can not set the acceleration, otherwise the mode switching speed can not be limited in time.
2025-08-12 增加设备串口输出流__fputs接口
2026-03-07 完善README说明文档
    [Motor35-BOM.csv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]
2026-03-07 motor_control中断频率较高达到20KHz,导致main主循环不执行,导致运行转速不准
